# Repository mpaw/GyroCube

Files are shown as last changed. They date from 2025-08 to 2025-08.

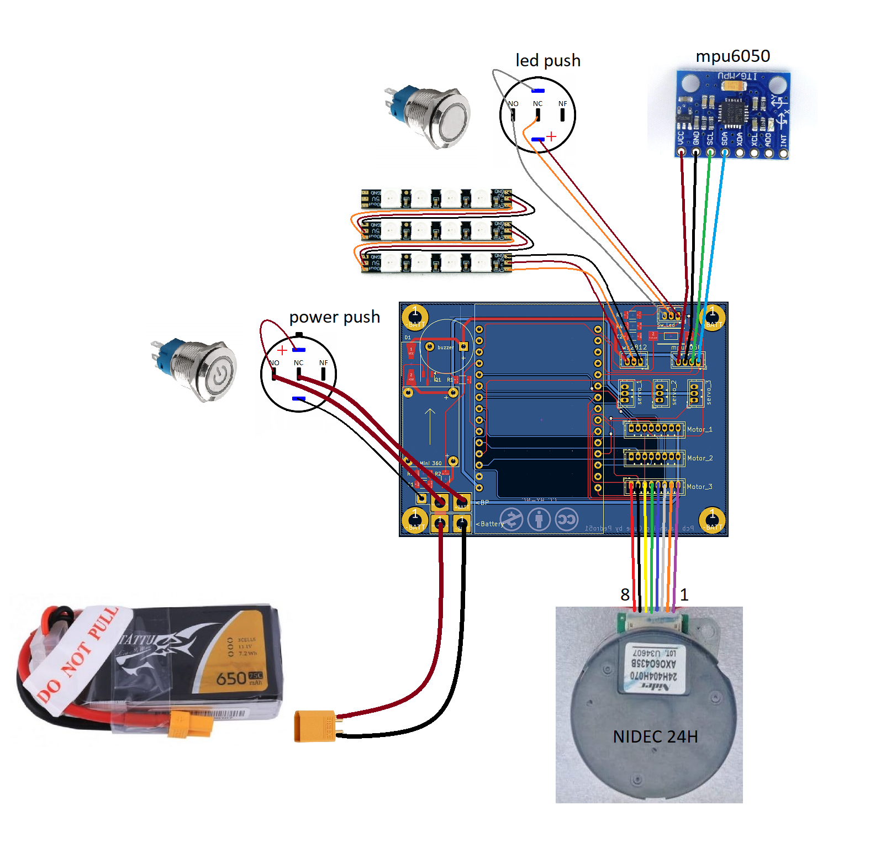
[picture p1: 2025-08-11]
PCB&Schemas/Wiring diagram.PNG

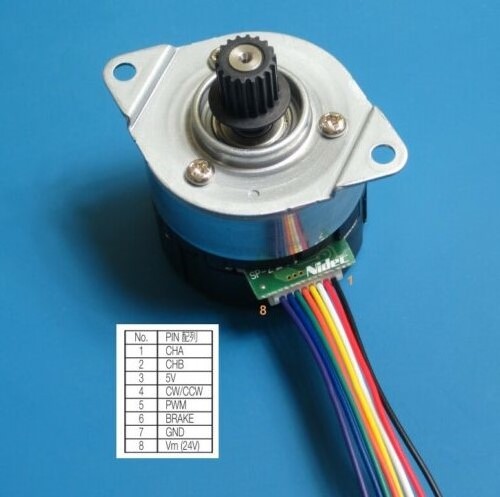
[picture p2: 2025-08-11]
PCB&Schemas/nidec.jpg

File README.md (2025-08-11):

# GyroCube
Self Balancing Cube Project

Balancing Cube project based on the "remrc" model: https://www.thingiverse.com/thing:6695891

    Creation of an Application to facilitate calibration and motor testing,
    Merging the main program with the motors test program,
    Creation of a printed circuit for those who wish to have a beautiful object,
    Addition of a Power button,
    Addition of a button to turn on the LEDs and change their colors,
    Modified the face files for placing the switches in 12 and 16mm. Thanks to dinomight.

Explanatory video: https://youtu.be/zuOgj580Nhk<br>
Led function video: https://youtu.be/vczHyelNjr4<br>
PCB: https://www.pcbway.com/project/shareproject/GyroCube_v1_1_5d583cf0.html<br>
Android app: [French](Appli%20APK/Cube_1_01_fr.apk),[English](Appli%20APK/Cube_1_01_en.apk)<br>
Browser BLE Config Tool: https://Pedro-51.github.io/GyroCube

#######################################################################################

For the program to work, you need to install esp32 by expressif v2.0.17 board version

#######################################################################################

## 12-5-2024 (Dinomight/Darkmadda)

Added new [BLE firmware](esp32_cube_vBLE_en/) this has a browser based config tool (can be use on android/mac/pc via chrome). The firmware is written to be used with platformio rather than the arduino ide. it may still work the arduino ide but i'm not sure (Platformio is far superior anyways). This firmware is backwards compatible with other app config methods (Bluetooth Serial, Pedro android app). I however think the new BLE tool is superior. I'm a little biased but try it you'll see.

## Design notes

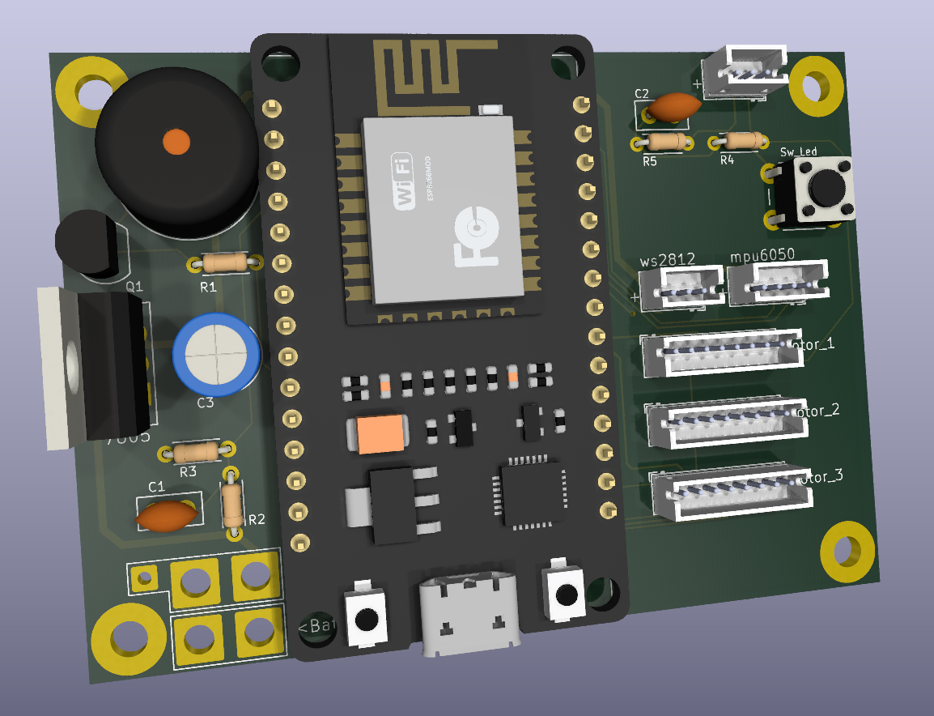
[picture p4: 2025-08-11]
PCB&Schemas/PCB_Std/3D_Std.PNG

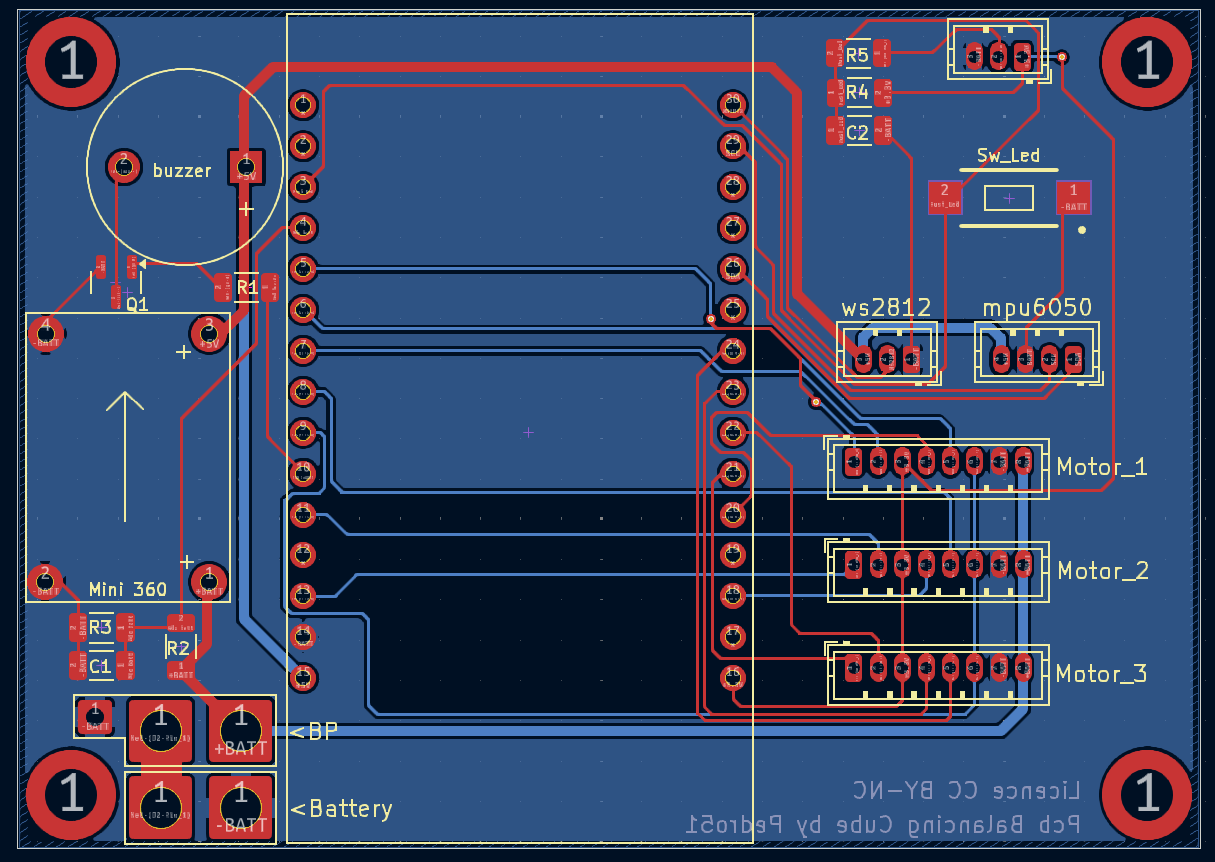
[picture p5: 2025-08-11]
PCB&Schemas/PCB_Smd/PCB_Smd.PNG

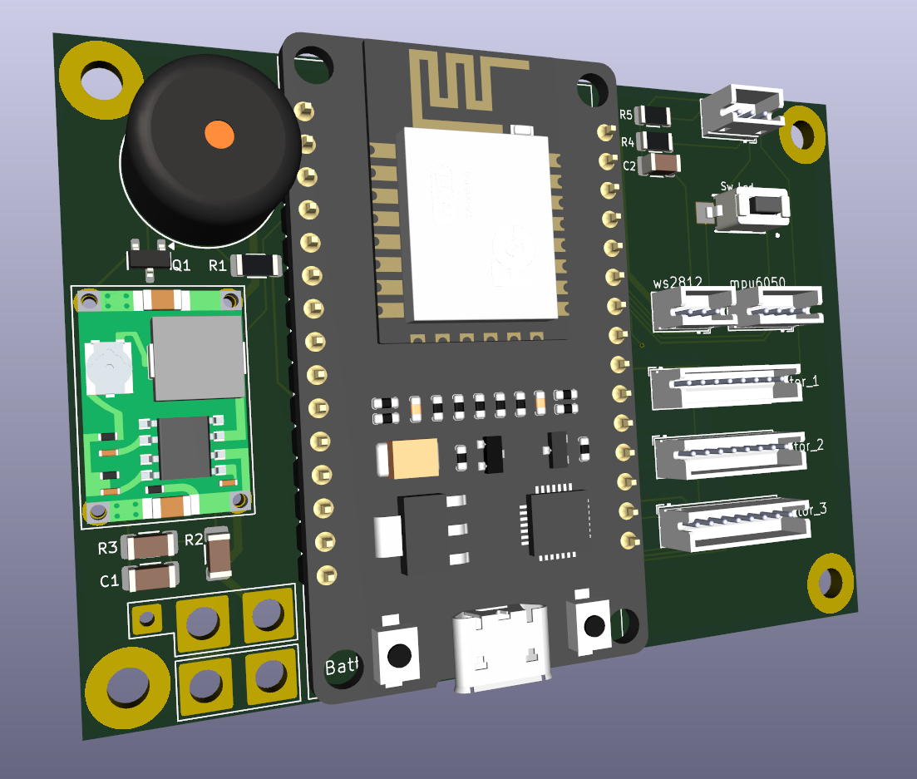
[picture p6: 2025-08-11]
PCB&Schemas/PCB_Smd/3D_Smd.png

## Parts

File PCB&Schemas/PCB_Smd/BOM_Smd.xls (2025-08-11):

Reference | Packages | Value | Qty | Comments
BT1 |  | Battery lipo 3s 650mah | 1
BZ1 |  | Buzzer 5v | 1
C1,C2 | 1206 SMD | 100nf | 2
J6,J7,J8 | JST-ZH 15cm | Connector jst-zh 01x08 double head | 3
J13 | JST-ZH 10cm | Connector jst-zh 01x03 with wire | 1
J12 | JST-ZH 10cm | Connector jst-zh 01x04 with wire | 1
Q1 | Sot-23-3 | MMBT2222A | 1
R1,R5 | 1206 SMD | 1k | 2
R2 | 1206 SMD | 33k | 1
R3,R4 | 1206 SMD | 10k | 2
SW1 | Ø16mm or Ø12mm 12-24v | Latch power inox switch | 1
SW2-1 | Ø16mm or Ø12mm 3-6v | Momentary inox switch | 1
SW2-2 |  | SMD switch reset Push | 1
U1 | mini360 | DC-DC 5v step down | 1
U2 | 30pin-micro module | esp32-wroom-32D cp2102 | 1
PCB | PCBway | PCB by Pedro51 | 1 | GyroCube_v1_2_Smd (https://www.pcbway.com/project/shareproject/GyroCube_v1_1_5d583cf0.html)
Wire | Silicon black wire | 16 AWG 100mm | 1
Wire | Silicon red wire | 16 AWG 100mm | 1
Wire | Silicon black wire | 24 AWG 100mm | 1
MPU6050 |  | Gyroscope | 1
WS1812 Led | Strip pcb for drone | Leds RGB PandaRC | 1
NIDEC 24H |  | Encoder Motor | 3
Battery Plug | Male | XT30 | 1
Screws | countersunk head screws | M4x8mm | 72
Screws | round head screw | M4x10mm | 12
Nuts | - | M4 | 144
Screws | countersunk head screws | M3x10mm | 36
Screws | countersunk head screws | M3x14mm | 12
Nuts | - | M3 | 52

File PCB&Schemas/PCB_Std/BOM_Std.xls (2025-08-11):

Reference | Packages | Value | Qty | Comments
BT1 |  | Battery lipo 3s 650mah | 1
BZ1 |  | Buzzer 5v | 1
C1,C2 | ceramic | 100nf-50v | 2
C3 | Polarized chimic | 100uf-10v | 1
J6,J7,J8 | JST-ZH 15cm | Connector jst-zh 01x08 double head | 3
J13 | JST-ZH 10cm | Connector jst-zh 01x03 with wire | 1
J12 | JST-ZH 10cm | Connector jst-zh 01x04 with wire | 1
Q1 | TO92 | 2n2222 | 1
R1,R5 | 1/4w | 1k | 2
R2 | 1/4w | 33k | 1
R3,R4 | 1/4w | 10k | 2
SW1 | Ø16mm or Ø12mm 12-24v | Latch power inox switch | 1
SW2-1 | Ø16mm or Ø12mm 3-6v | Momentary inox switch | 1
SW2-2 |  | switch reset Push | 1
U1 | TO220 | LM7805 DC-DC 5v regulator | 1
U2 | 30pin-micro module | esp32-wroom-32D cp2102 | 1
PCB | PCBway | PCB by Pedro51 | 1 | GyroCube_v1_2_Std (https://www.pcbway.com/project/shareproject/GyroCube_v1_2_Smd_9171484b.html)
Wire | Silicon black wire | 16 AWG 100mm | 1
Wire | Silicon red wire | 16 AWG 100mm | 1
Wire | Silicon black wire | 24 AWG 100mm | 1
MPU6050 |  | Gyroscope | 1
WS1812 Led | Strip pcb for drone | Leds RGB PandaRC | 1
NIDEC 24H |  | Encoder Motor | 3
Battery Plug | Male | XT30 | 1
Screws | countersunk head screws | M4x8mm | 72
Screws | round head screw | M4x10mm | 12
Nuts | - | M4 | 144
Screws | countersunk head screws | M3x10mm | 36
Screws | countersunk head screws | M3x14mm | 12
Nuts | - | M3 | 52

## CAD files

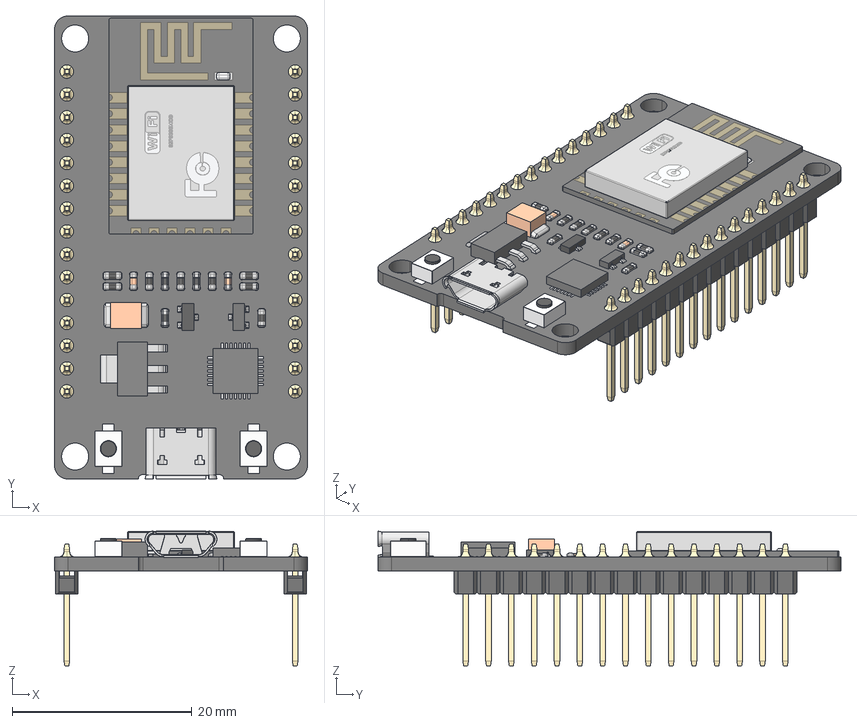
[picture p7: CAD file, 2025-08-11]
PCB&Schemas/PCB_Smd/Kidad_PCB_Smd/3d_Model/esp32_dev_kit_v1_asm.stp
28.1 x 51.5 x 15.0 mm
PCB
PIN x 30
WIFI_CARD_2
RECTANGULARCHIP_2
MICROCHIP_2
TANCHIP_2
TRANSISTOR_3-LEG_2
RESISTOR1_2 x 11
RESISTOR2-32_2 x 2
TRANSISTOR_3-LEG2_2
BUTTONFLASH-13_2 x 2
BUTTONFLASH-14_2 x 2
USB_SOCKET_2

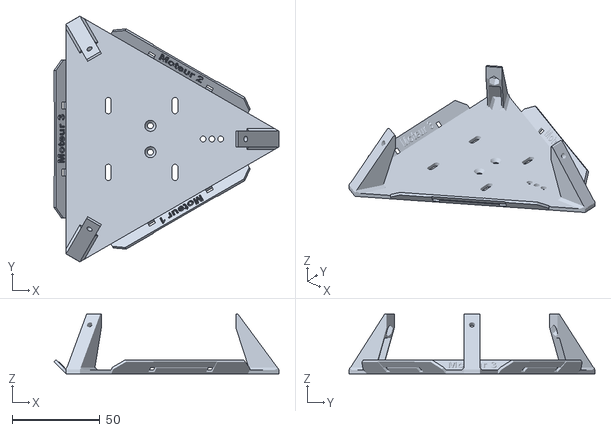
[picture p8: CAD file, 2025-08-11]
3D_files/cubli_midplate_v3_1x.stl
128.1 x 139.9 x 34.1

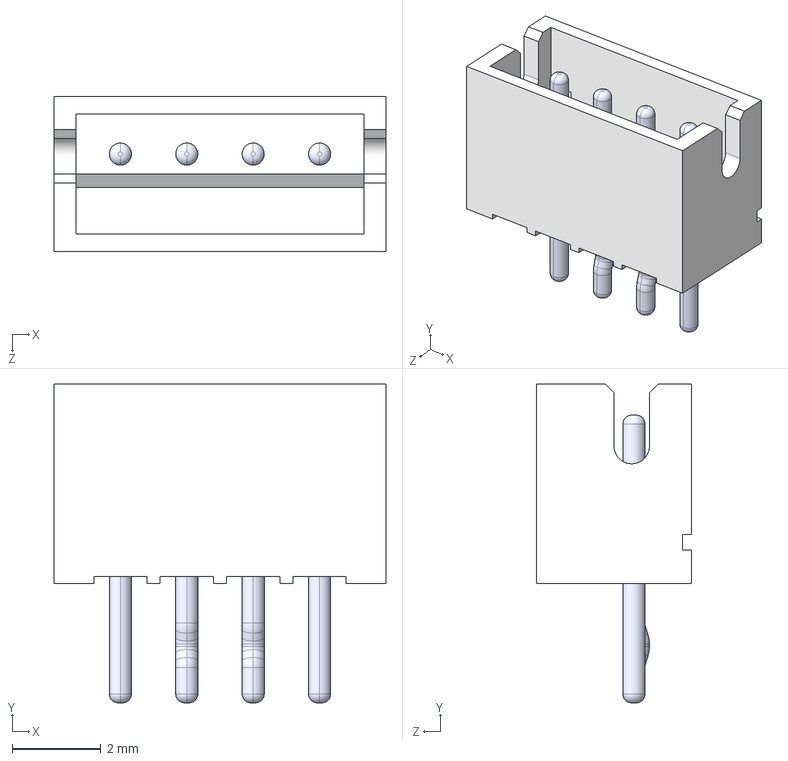
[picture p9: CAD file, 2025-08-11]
PCB&Schemas/PCB_Smd/Kidad_PCB_Smd/3d_Model/B4B-ZR--3DModel-STEP-56544.STEP
7.50 x 7.20 x 3.50 mm
BxB-ZR_4
pin_straight x 2
pin_Bent x 2

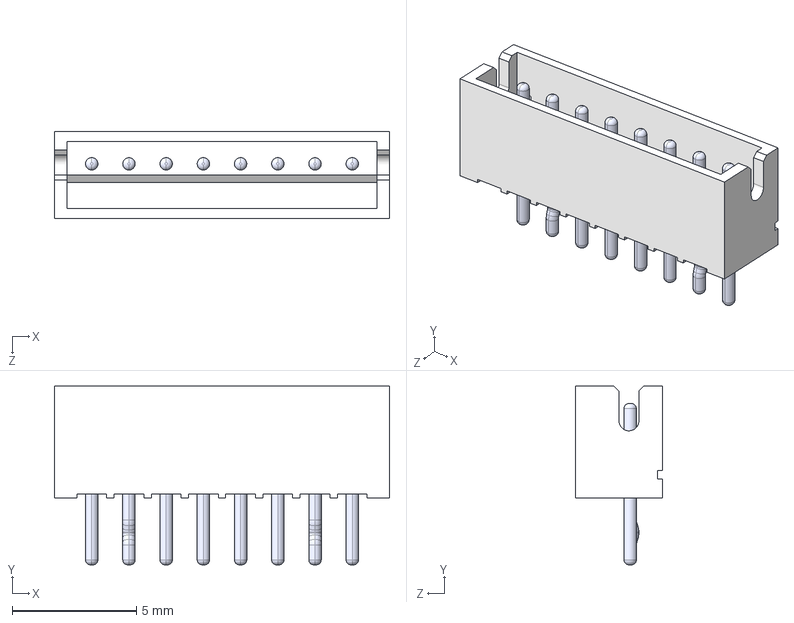
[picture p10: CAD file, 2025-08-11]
PCB&Schemas/PCB_Std/Kicad_PCB_Std/3d_Model/B8B-ZR -LF--SN---3DModel-STEP-56544.STEP
13.5 x 7.20 x 3.50 mm
BxB-ZR_8
pin_straight x 6
pin_Bent x 2

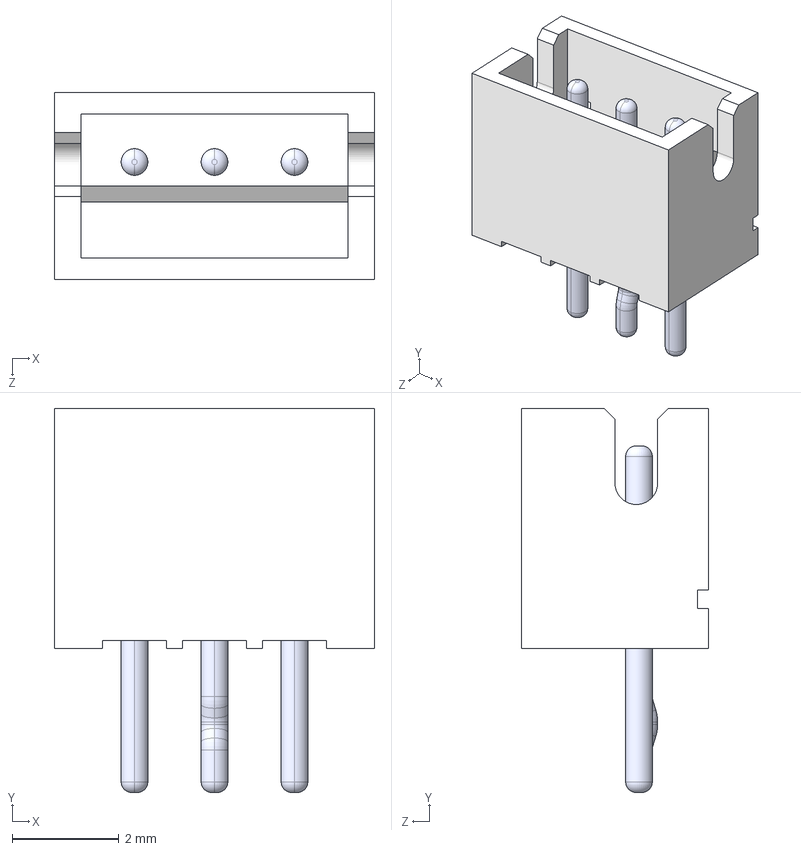
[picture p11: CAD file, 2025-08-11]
PCB&Schemas/PCB_Smd/Kidad_PCB_Smd/3d_Model/B3B-ZR--3DModel-STEP-56544.STEP
6.00 x 7.20 x 3.50 mm
BxB-ZR_3
pin_straight x 2
pin_Bent

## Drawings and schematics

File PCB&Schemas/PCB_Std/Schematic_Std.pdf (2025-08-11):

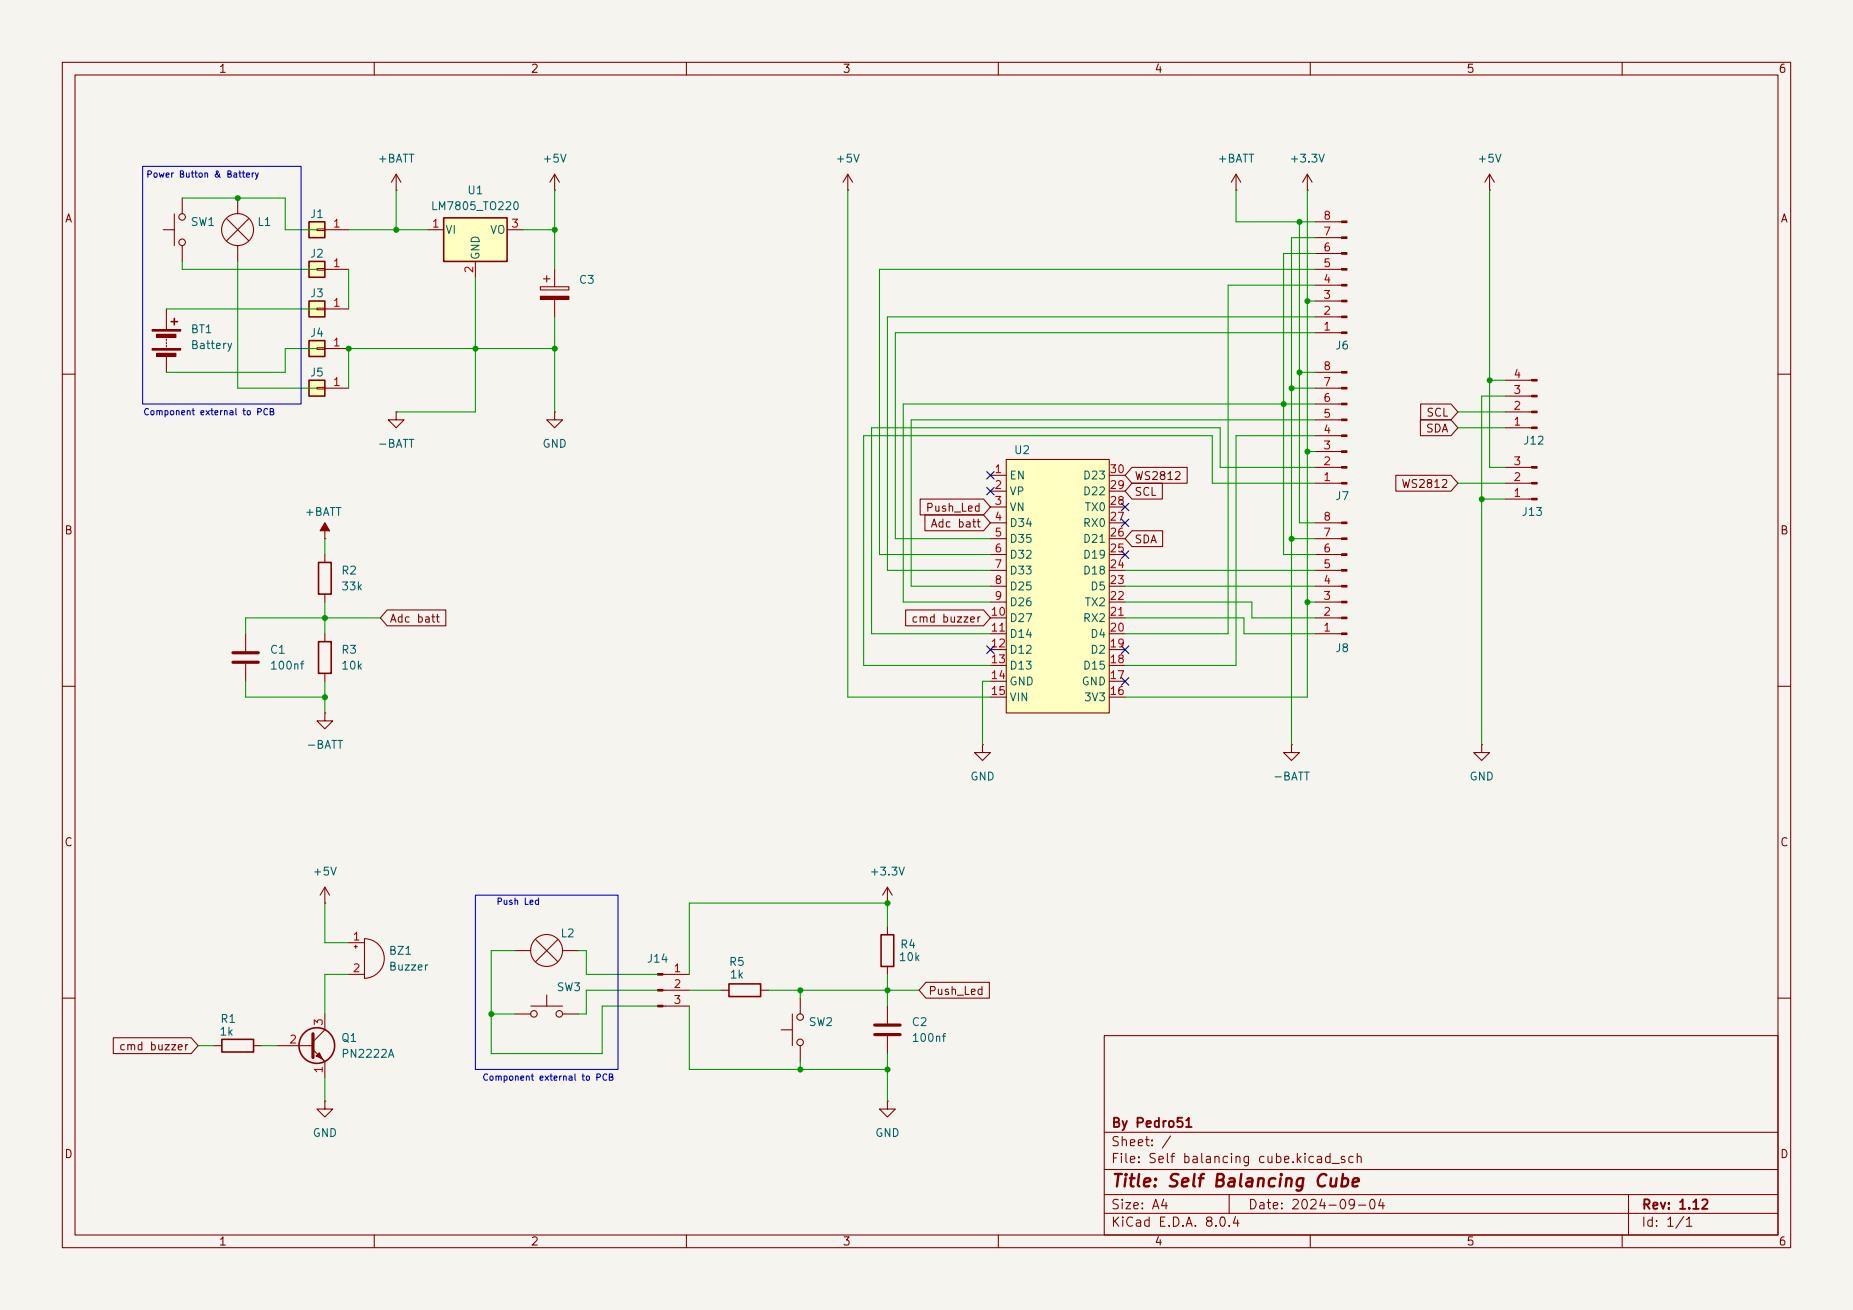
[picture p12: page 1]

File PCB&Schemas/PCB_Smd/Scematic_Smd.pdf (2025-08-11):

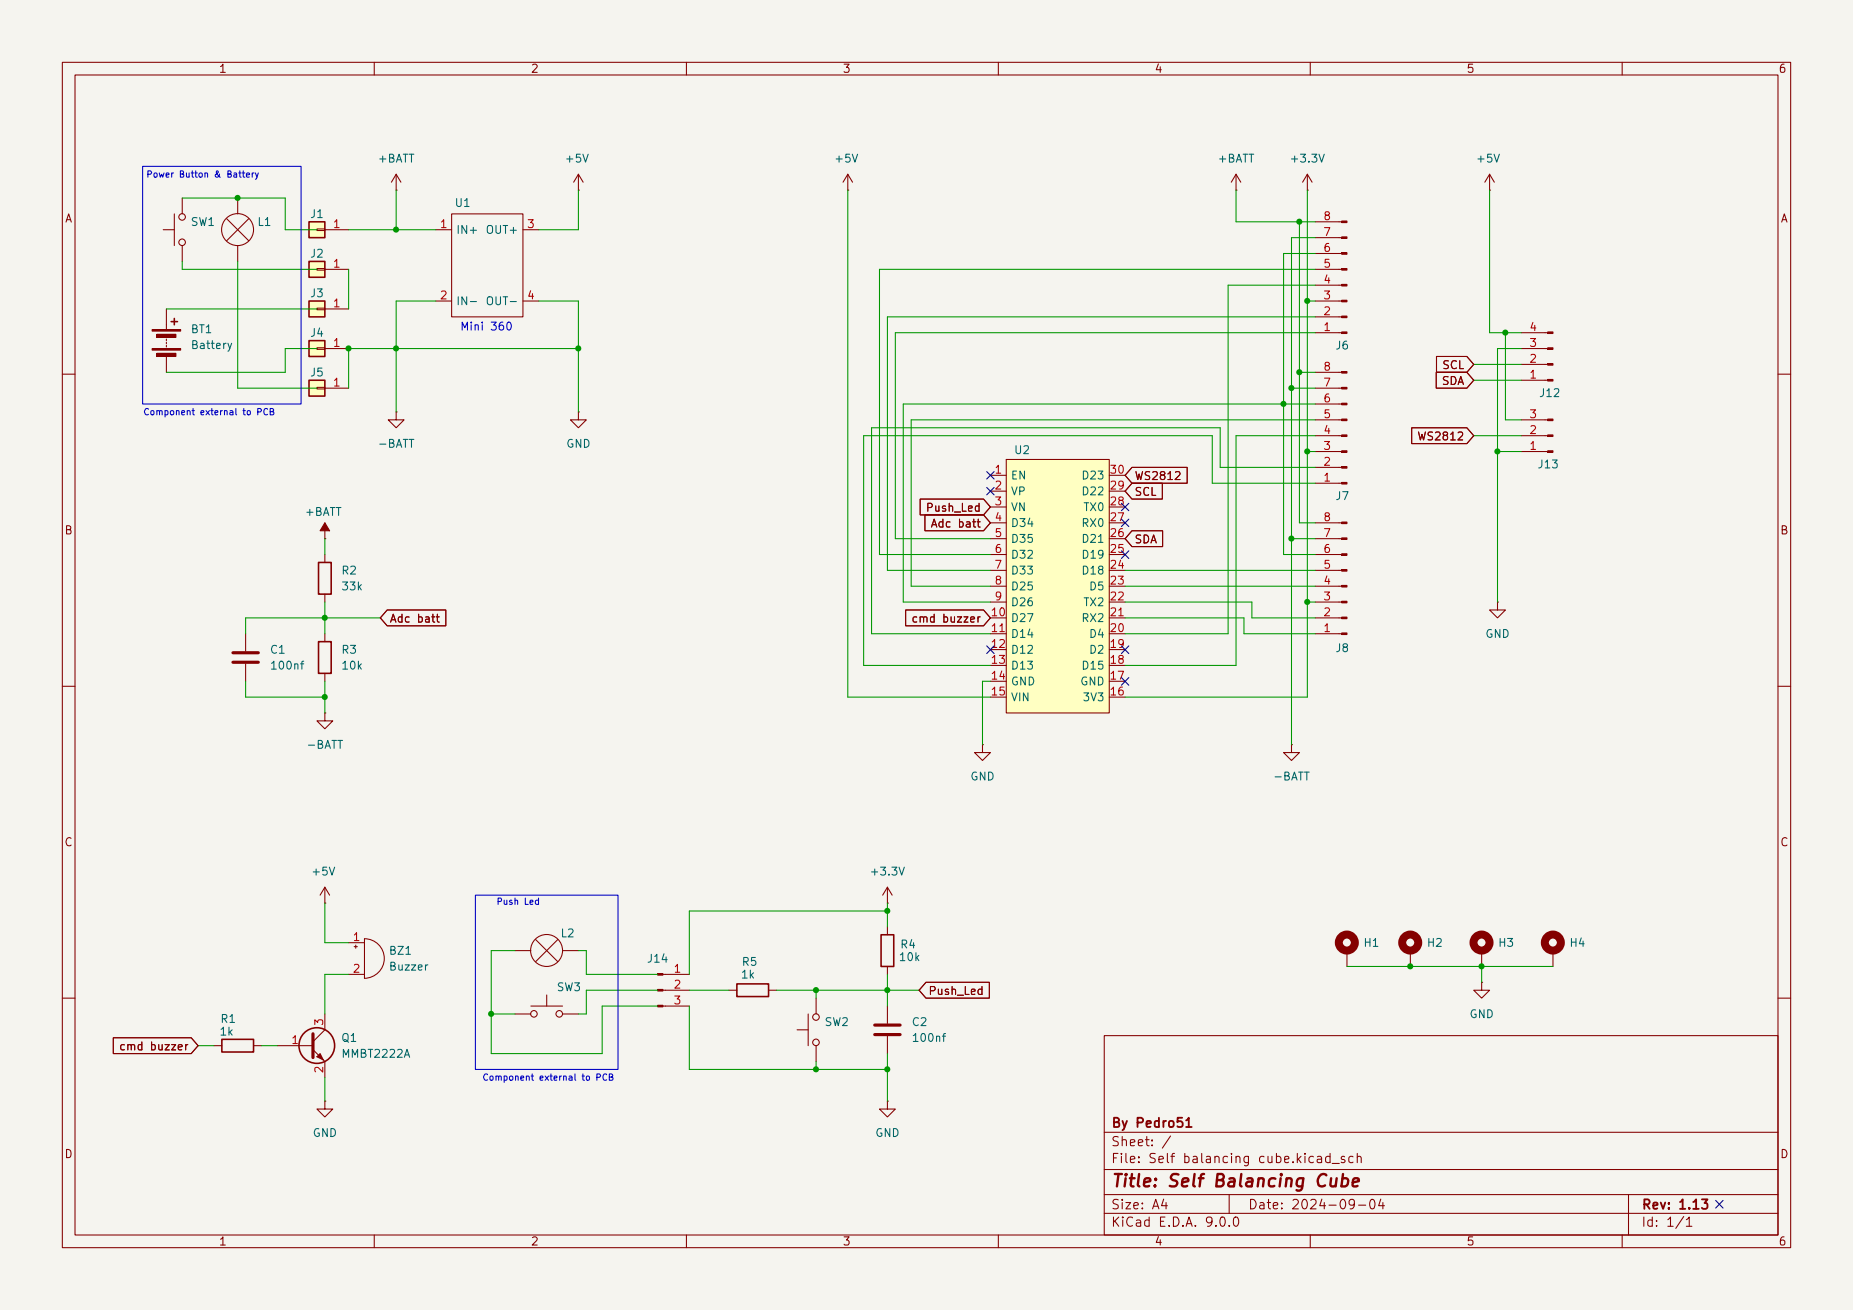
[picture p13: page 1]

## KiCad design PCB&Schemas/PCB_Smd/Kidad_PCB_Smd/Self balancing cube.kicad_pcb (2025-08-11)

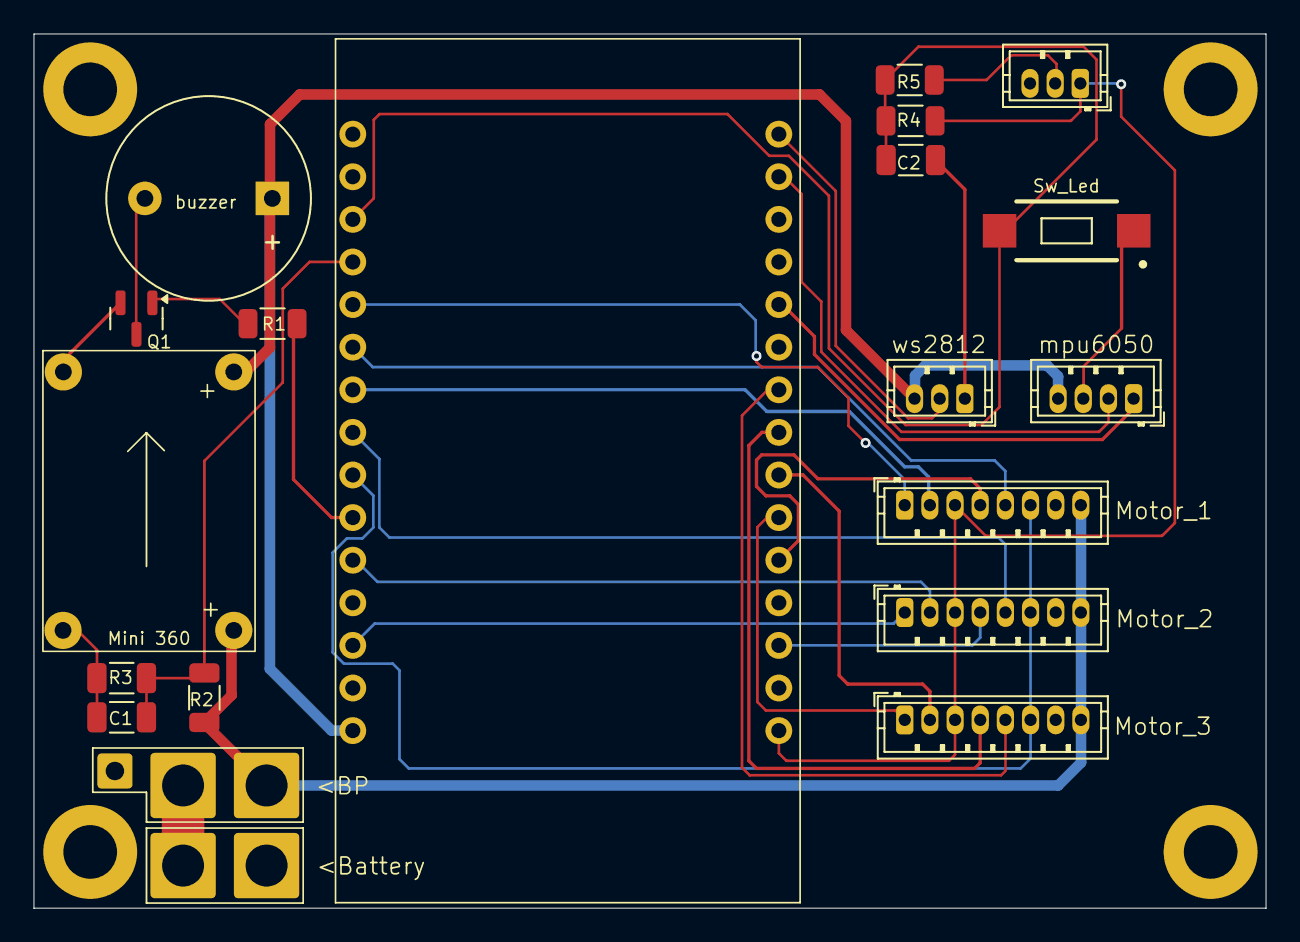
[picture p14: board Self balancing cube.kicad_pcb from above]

Board: 2 copper layers, 73.5 x 52.1 mm, 27 parts (0 on the bottom side), 27 nets.

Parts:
BZ1: Buzzer; Buzzer_12x9.5RM7.6
C1, C2: 100nf; C_1206_3216Metric
H1, H2, H3, H4: MountingHole; MountingHole_3.2mm_M3_DIN965_Pad
J1, J2, J3, J4: Conn_01x01; SolderWire-2sqmm_1x01_D2mm_OD3.9mm
J5: Conn_01x01; SolderWire-0.5sqmm_1x01_D0.9mm_OD2.1mm
J6, J7, J8: Conn_01x08_Pin; JST_ZH_B8B-ZR_1x08_P1.50mm_Vertical
J12: Conn_01x04_Pin; JST_ZH_B4B-ZR_1x04_P1.50mm_Vertical
J13, J14: Conn_01x03_Pin; JST_ZH_B3B-ZR_1x03_P1.50mm_Vertical
Q1: MMBT2222A; SOT-23
R1, R5: 1k; R_1206_3216Metric
R2: 33k; C_1206_3216Metric
R3: 10k; C_1206_3216Metric
R4: 10k; R_1206_3216Metric
SW2: SW_Push; SW_RS-032G05A3-SMRT
U1: 5v; DCDC buck
U2: esp module 30pins

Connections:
+3.3V: J6.3, J7.3, J8.3, J14.1, R4.2, U2.16 (3V3)
+5V: BZ1.1 (+), J12.4, J13.3, U1.3 (OUT+), U2.15 (VIN)
+BATT: J1.1, J6.8, J7.8, J8.8, R2.1, U1.1 (IN+)
-BATT: C1.2, C2.2, H1.1, H2.1, H3.1, H4.1, J4.1, J5.1, J6.7, J7.7, J8.7, J12.3, J13.1, J14.3, Q1.2 (E), R3.2, SW2.1, U1.2 (IN-), U1.4 (OUT-), U2.14 (GND)
Adc batt: C1.1, R2.2, R3.1, U2.4 (D34)
unnamed: BZ1.2 (-), Q1.3 (C)
unnamed: J2.1, J3.1
unnamed: J6.1, U2.5 (D35)
unnamed: J6.2, U2.7 (D33)
unnamed: J6.4, U2.20 (D4)
unnamed: J6.5, U2.6 (D32)
unnamed: J6.6, J7.6, J8.6, U2.9 (D26)
unnamed: J7.1, U2.13 (D13)
unnamed: J7.2, U2.11 (D14)
unnamed: J7.4, U2.18 (D15)
unnamed: J7.5, U2.8 (D25)
unnamed: J8.1, U2.21 (RX2)
unnamed: J8.2, U2.22 (TX2)
unnamed: J8.4, U2.23 (D5)
unnamed: J8.5, U2.24 (D18)
unnamed: J14.2, R5.1
unnamed: Q1.1 (B), R1.2
Push_Led: C2.1, R4.1, R5.2, SW2.2, U2.3 (VN)
SCL: J12.2, U2.29 (D22)
SDA: J12.1, U2.26 (D21)
WS2812: J13.2, U2.30 (D23)
cmd buzzer: R1.1, U2.10 (D27)

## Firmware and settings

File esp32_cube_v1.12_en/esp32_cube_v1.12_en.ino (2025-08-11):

#include "ESP32.h"
#include <Wire.h>
#include <EEPROM.h>
#include "BluetoothSerial.h"
#include <FastLED.h>

BluetoothSerial SerialBT; 
CRGB leds[NUM_PIXELS];

void setup() {
  Serial.begin(115200);
  SerialBT.begin("ESP32-Cube");
  EEPROM.begin(EEPROM_SIZE);
  
  FastLED.addLeds<WS2812B, LED_PIN, RGB>(leds, NUM_PIXELS);  // GRB ordering is typical
  
  pinMode(BUZZER, OUTPUT);
  pinMode(BRAKE, OUTPUT);
  digitalWrite(BRAKE, HIGH);
  pinMode(INT_LED, INPUT);

  for (i=0;i<250;i+=10){ colorLed(i, i, 0, 1, 12, 0);}
  for (RGB_val=0;RGB_val<18;RGB_val++){
    Red = RGB_Color[RGB_val][0]; Green = RGB_Color[RGB_val][1]; Blue  = RGB_Color[RGB_val][2];
    colorLed(Red, Green, Blue, 1, 12, 80); //Red, Green, Blue, FirstPixel, LastPixel, Delay
  }
  for (i=250;i>0;i-=10){colorLed(i, i*0.68, 0, 1, 12, 5);}
  colorLed(0, 0, 0, 1, 12, 0);
  
  pinMode(DIR1, OUTPUT);
  pinMode(ENC1_1, INPUT);
  pinMode(ENC1_2, INPUT);
  attachInterrupt(ENC1_1, ENC1_READ, CHANGE);
  attachInterrupt(ENC1_2, ENC1_READ, CHANGE);
  ledcSetup(PWM1_CH, BASE_FREQ, TIMER_BIT);
  ledcAttachPin(PWM1, PWM1_CH);
  Motor1_control(0);
  
  pinMode(DIR2, OUTPUT);
  pinMode(ENC2_1, INPUT);
  pinMode(ENC2_2, INPUT);
  attachInterrupt(ENC2_1, ENC2_READ, CHANGE);
  attachInterrupt(ENC2_2, ENC2_READ, CHANGE);
  ledcSetup(PWM2_CH, BASE_FREQ, TIMER_BIT);
  ledcAttachPin(PWM2, PWM2_CH);
  Motor2_control(0);
  
  pinMode(DIR3, OUTPUT);
  pinMode(ENC3_1, INPUT);
  pinMode(ENC3_2, INPUT);
  attachInterrupt(ENC3_1, ENC3_READ, CHANGE);
  attachInterrupt(ENC3_2, ENC3_READ, CHANGE);
  ledcSetup(PWM3_CH, BASE_FREQ, TIMER_BIT);
  ledcAttachPin(PWM3, PWM3_CH);
  Motor3_control(0);

  EEPROM.get(0, offsets);
  //offsets.ID = 0; // for debug
  if(offsets.ID == 255){
    offsets.ID = 0;
    offsets.Red = Red; offsets.Green = Green; offsets.Blue = Blue; offsets.RGB_val = RGB_val;
    offsets.K1 = K1; offsets.K2 = K2; offsets.K3 = K3; offsets.K4 = K4; offsets.zK2 = zK2; offsets.zK3 = zK3;
    offsets.eK1 = eK1; offsets.eK2 = eK2; offsets.eK3 = eK3; offsets.eK4 = eK4;
    save();
  }else if (offsets.ID == 96){
    Red = offsets.Red; Green = offsets.Green; Blue = offsets.Blue;
    K1 = offsets.K1; K2 = offsets.K2; K3 = offsets.K3; K4 = offsets.K4; zK2 = offsets.zK2; zK3 = offsets.zK3;
    eK1 = offsets.eK1; eK2 = offsets.eK2; eK3 = offsets.eK3; eK4 = offsets.eK4;
    calibrated = true;
  }

  angle_setup();
}

void loop() {
  currentT = millis();
  if (currentT - previousT_1 >= loop_time) {
    Tuning();
    angle_calc();
        
    motor1_speed = enc_count1;
    enc_count1 = 0;
    motor2_speed = enc_count2;
    enc_count2 = 0;
    motor3_speed = enc_count3;
    enc_count3 = 0;
    

  if (Mode == 0){

    threeWay_to_XY(motor1_speed, motor2_speed, motor3_speed);
    motors_speed_Z = motor1_speed + motor2_speed + motor3_speed;
    
    if (vertical_vertex && calibrated && !calibrating) {    
      digitalWrite(BRAKE, HIGH);
      gyroX = GyX / 131.0;
      gyroY = GyY / 131.0;
      gyroZ = GyZ / 131.0;
      gyroXfilt = alpha * gyroX + (1 - alpha) * gyroXfilt;
      gyroYfilt = alpha * gyroY + (1 - alpha) * gyroYfilt;
      
      int pwm_X = constrain(K1 * robot_angleX + K2 * gyroXfilt + K3 * speed_X + K4 * motors_speed_X, -255, 255);
      int pwm_Y = constrain(K1 * robot_angleY + K2 * gyroYfilt + K3 * speed_Y + K4 * motors_speed_Y, -255, 255);
      int pwm_Z = constrain(zK2 * gyroZ + zK3 * motors_speed_Z, -255, 255);

      motors_speed_X += speed_X / 5; 
      motors_speed_Y += speed_Y / 5;
      XYZ_to_threeWay(-pwm_X, pwm_Y, -pwm_Z);
      
    } else if (vertical_edge && calibrated && !calibrating) {
      digitalWrite(BRAKE, HIGH);
      gyroX = GyX / 131.0;
      gyroXfilt = alpha * gyroX + (1 - alpha) * gyroXfilt;
      
      int pwm_X = constrain(eK1 * robot_angleX + eK2 * gyroXfilt + eK3 * motor3_speed + eK4 * motors_speed_X, -255, 255);
      
      motors_speed_X += motor3_speed / 5;
      Motor3_control(pwm_X);
      
    } else {
      XYZ_to_threeWay(0, 0, 0);
      digitalWrite(BRAKE, LOW);
      motors_speed_X = 0;
      motors_speed_Y = 0; 
      
      if  (calibrated && !calibrating) {
        RGB_Process();
      }
    }
  }

  if (Mode == 1 ){
      switch (f) {
        case 1:
          colorLed(50, 50, 50, 1, 4, 0);
          digitalWrite(BRAKE, HIGH);
          if (lock) Serial.println("Test moteur 1."); SerialBT.println("46");
          Motor1_control(50);
          break;
        case 4:
          digitalWrite(BRAKE, LOW);
          if (lock) Serial.println("Stop."); SerialBT.println("41");
          Motor1_control(0);
          break;      
        case 7:
          digitalWrite(BRAKE, HIGH);
          if (lock) Serial.println("Changement direction..."); SerialBT.println("42");
          Motor1_control(-50);
          break;
        case 10:
          digitalWrite(BRAKE, LOW);
          if (lock) Serial.println("Stop."); SerialBT.println("41");
          Motor1_control(0);
          break; 
        case 13:
          digitalWrite(BRAKE, HIGH);
          if (lock) Serial.println("Check de l'encodeur..."); SerialBT.println("43");
          Motor1_control(70);
          break; 
        case 16:
          digitalWrite(BRAKE, LOW);
          if (lock && motor1_speed > 300) {
            Serial.println("Encodeur OK."); 
            Serial.print("Vitesse: "); Serial.println(motor1_speed);
            s1.concat(motor1_speed);
            SerialBT.println("44"  + s1);
            Serial.println("Stop.");
          } else if (lock && motor1_speed <= 0) {
            Serial.println("Encodeur FAIL.");
            Serial.print("Vitesse: "); Serial.println(motor1_speed);
            s1.concat(motor1_speed);
            SerialBT.println("45"  + s1);
            Serial.println("Stop.");
          }
          s1 = "";
          Motor1_control(0);
          colorLed(0, 0, 0, 1, 4, 0);
          break;      
  
        case 19:
          colorLed(50, 50, 50, 5, 8, 0);
          digitalWrite(BRAKE, HIGH);
          if (lock) Serial.println("Test moteur 2."); SerialBT.println("47");
          Motor2_control(50);
          break;
        case 22:
          digitalWrite(BRAKE, LOW);
          if (lock) Serial.println("Stop."); SerialBT.println("41");
          Motor2_control(0);
          break;      
        case 25:
          digitalWrite(BRAKE, HIGH);
          if (lock) Serial.println("Changement direction..."); SerialBT.println("42");
          Motor2_control(-50);
          break;
        case 28:
          digitalWrite(BRAKE, LOW);
          if (lock) Serial.println("Stop."); SerialBT.println("41");
          Motor2_control(0);
          break; 
        case 31:
          digitalWrite(BRAKE, HIGH);
          if (lock) Serial.println("Check de l'encodeur..."); SerialBT.println("43");
          Motor2_control(70);
          break; 
        case 34:
          digitalWrite(BRAKE, LOW);
          if (lock && motor2_speed > 300) {
            Serial.println("Encodeur OK.");
            Serial.print("Vitesse: "); Serial.println(motor2_speed);
            s1.concat(motor2_speed);
            SerialBT.println("44"  + s1);
            Serial.println("Stop.");
          } else if (lock && motor2_speed <= 0) {
            Serial.println("Encodeur FAIL.");
            Serial.print("Vitesse: "); Serial.println(motor2_speed);
            s1.concat(motor2_speed);
            SerialBT.println("45"  + s1);
            Serial.println("Stop.");
          }
          s1 = "";
          Motor2_control(0);
          colorLed(0, 0, 0, 5, 8, 0);
          break;        
  
        case 37:
          colorLed(50, 50, 50, 9, 12, 0);
          digitalWrite(BRAKE, HIGH);
          if (lock) Serial.println("Test moteur 3."); SerialBT.println("48");
          Motor3_control(50);
          break;
        case 40:
          digitalWrite(BRAKE, LOW);
          if (lock) Serial.println("Stop."); SerialBT.println("41");
          lock = 0;
          Motor3_control(0);
          break;      
        case 43:
          digitalWrite(BRAKE, HIGH);
          if (lock) Serial.println("Changement direction..."); SerialBT.println("42");
          Motor3_control(-50);
          break;
        case 46:
          digitalWrite(BRAKE, LOW);
          if (lock) Serial.println("Stop."); SerialBT.println("41");
          Motor3_control(0);
          break; 
        case 49:
          digitalWrite(BRAKE, HIGH);
          if (lock) Serial.println("Check de l'encodeur..."); SerialBT.println("43");
          Motor3_control(70);
          break; 
        case 52:
          digitalWrite(BRAKE, LOW);
          if (lock && motor3_speed > 300) {
            Serial.println("Encodeur OK.");
            Serial.print("Vitesse: "); Serial.println(motor3_speed);
            s1.concat(motor3_speed);
            SerialBT.println("44"  + s1);
            Serial.println("Stop.");
          } else if (lock && motor3_speed <= 0) {
            Serial.println("Encodeur FAIL.");
            Serial.print("Vitesse: "); Serial.println(motor3_speed);
            s1.concat(motor3_speed);
            SerialBT.println("45"  + s1);
            Serial.println("Stop.");
          }
          s1 = "";
          Motor3_control(0);
          colorLed(0, 0, 0, 9, 12, 0);
          break;        
        }
        lock = 0;
  }
    
  previousT_1 = currentT;
}    
  if (currentT - previousT_2 >= 1000) {

    battVoltage((double)analogRead(VBAT) / 204); // value 204 must be selected by measuring battery voltage!
    
    if (!calibrated && !calibrating) {
      Serial.println("Tu doit d'abord procéder au calibrage des points d'équilibres...");
      SerialBT.println("95");
      if (!calibrated_leds) {
        colorLed(0, 50, 0, 1, 12, 0); 
        calibrated_leds = true; 
      } else {
         (0, 0, 0, 1, 12, 0); 
        calibrated_leds = false; 
      }
    }
    
    if (Mode == 1){
      f++; 
      if (f == 53){ beep(); Serial.println("Fin des tests Moteurs."); SerialBT.println("96"); f = 1; Mode = 0;} 
    lock = 1;
    }
    previousT_2 = currentT;
  }
  
  if (ConnectBT == true && (currentT - previousT_3) > DelayBT)
      {
        init_BT();
        ConnectBT = false;
      }
}

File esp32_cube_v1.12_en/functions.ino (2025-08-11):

void writeTo(byte device, byte address, byte value) {
  Wire.beginTransmission(device);
  Wire.write(address);
  Wire.write(value);
  Wire.endTransmission(true);
}

void beep() {
    digitalWrite(BUZZER, HIGH);
    delay(2);
    digitalWrite(BUZZER, LOW);
    delay(80);
}
    
//***********************************************************************
// Initialise Bluetooth
//***********************************************************************
void init_BT()
{
        Mode = 0; loop_time = 15;
        calibrating = false;
        colorLed(0, 0, 0, 1, 12, 0);
        LedRGB = false;
}

//***********************************************************************
// Rgb Led Command
//***********************************************************************
void colorLed(int Red, int Green, int Blue , int firstled, int lastled, int wait) {
    for(int i = firstled-1; i < lastled; i++) {    // For each pixel in strip...
    leds[i] = CRGB(Red, Green, Blue);
    FastLED.show();                          //  Update strip to match
  }
    delay(wait);                           //  Pause for a moment
}

//***********************************************************************
// Rgb Led Process
//***********************************************************************
void RGB_Process(){
  j = 0;
  while (digitalRead(INT_LED) == LOW){
    if (Push == false){Push = true;}
    j++; delay (5);
    if (j >= 250){break;}
  }
  if (!ChooseColor){
    if (Push == true){
      if (j < 250){
        if (LedRGB == true){
          colorLed(0, 0, 0, 1, 12, 0);
          LedRGB = false;
        }else{
          colorLed(Red, Green, Blue, 1, 12, 0);
          LedRGB = true;
        }
        beep();
      }else{
        Push = false; LedRGB = true; 
        colorLed(Red, Green, Blue, 1, 12, 80);
        colorLed(0, 0, 0, 1, 12, 80);
        colorLed(Red, Green, Blue, 1, 12, 0); beep ();
        while (digitalRead(INT_LED) == LOW){}
        delay (5); ChooseColor = true;
      }
    }
  }else{
    if (Push == true){
      if (j < 250){
        if (RGB_val < 17){RGB_val++;}else{RGB_val = 0;}
        Red = RGB_Color[RGB_val][0]; Green = RGB_Color[RGB_val][1]; Blue = RGB_Color[RGB_val][2];
        colorLed(Red, Green, Blue, 1, 12, 0);
        Push = false;
        beep();
      }else{
        offsets.Red = Red; offsets.Green = Green; offsets.Blue = Blue; offsets.RGB_val = RGB_val;
        save();
        colorLed(0, 0, 0, 1, 12, 0); 
        beep (); colorLed(Red, Green, Blue, 1, 12, 0); 
        beep ();
        Push = false; ChooseColor = false;
      }
    }
  }
  while (digitalRead(INT_LED) == LOW){}
  if (Push == true){Push = false;}
  delay (5);
}

void save() {
    EEPROM.put(0, offsets);
    EEPROM.commit();
    beep();
}

void angle_setup() {
  Wire.begin();
  delay (100);
  writeTo(MPU6050, PWR_MGMT_1, 0);
  writeTo(MPU6050, ACCEL_CONFIG, accSens << 3); // Specifying output scaling of accelerometer
  writeTo(MPU6050, GYRO_CONFIG, gyroSens << 3); // Specifying output scaling of gyroscope
  delay (100);
  
  beep();
  colorLed(50, 0, 0, 9, 12, 0);
  for (int i = 0; i < 512; i++) {
    angle_calc();
    GyZ_offset_sum += GyZ;
    delay(5);
  }
  GyZ_offset = GyZ_offset_sum >> 9;
  Serial.print("GyZ offset value = "); Serial.println(GyZ_offset);
  beep();
  colorLed(0, 0, 0, 9, 12, 0);

  colorLed(50, 0, 0, 5, 8, 0);
  for (int i = 0; i < 512; i++) {
    angle_calc();
    GyY_offset_sum += GyY;
    delay(5);
  }
  GyY_offset = GyY_offset_sum >> 9;
  Serial.print("GyY offset value = "); Serial.println(GyY_offset);
  beep();
  colorLed(0, 0, 0, 5, 8, 0);

  colorLed(50, 0, 0, 1, 4, 0);
  for (int i = 0; i < 512; i++) {
    angle_calc();
    GyX_offset_sum += GyX;
    delay(5);
  }
  GyX_offset = GyX_offset_sum >> 9;
  Serial.print("GyX offset value = "); Serial.println(GyX_offset);
  colorLed(0, 0, 0, 1, 4, 150);
  beep();
  beep();
  colorLed(50, 0, 0, 1, 12, 300);
  colorLed(0, 0, 0, 1, 12, 150);
  colorLed(50, 0, 0, 1, 12, 300);
  colorLed(0, 0, 0, 1, 12, 0);
}

void angle_calc() {
  
  Wire.beginTransmission(MPU6050);
  Wire.write(0x43);
  Wire.endTransmission(false);
  Wire.requestFrom(MPU6050, 6, true);  
  GyX = Wire.read() << 8 | Wire.read();
  GyY = Wire.read() << 8 | Wire.read();
  GyZ = Wire.read() << 8 | Wire.read();

  Wire.beginTransmission(MPU6050);
  Wire.write(0x3B);                  
  Wire.endTransmission(false);
  Wire.requestFrom(MPU6050, 6, true); 
  AcX = Wire.read() << 8 | Wire.read();
  AcY = Wire.read() << 8 | Wire.read();
  AcZ = Wire.read() << 8 | Wire.read();

  if (abs(AcX) < 2000) {
    AcXc = AcX - offsets.acXv;
    AcYc = AcY - offsets.acYv;
    AcZc = AcZ - offsets.acZv;
  } else {
    AcXc = AcX - offsets.acXe;
    AcYc = AcY - offsets.acYe;
    AcZc = AcZ - offsets.acZe;
  }
  GyZ -= GyZ_offset;
  GyY -= GyY_offset;
  GyX -= GyX_offset;

  robot_angleY += GyY * loop_time / 1000 / 65.536;
  Acc_angleY = atan2(AcXc, -AcZc) * 57.2958;
  robot_angleY = robot_angleY * Gyro_amount + Acc_angleY * (1.0 - Gyro_amount);

  robot_angleX += GyX * loop_time / 1000 / 65.536;
  Acc_angleX = -atan2(AcYc, -AcZc) * 57.2958;
  robot_angleX = robot_angleX * Gyro_amount + Acc_angleX * (1.0 - Gyro_amount);

  //Serial.print("AcX= "); Serial.print(AcX); Serial.print("  AcY= "); Serial.print(AcY); Serial.print("  AcZ= "); Serial.println(AcZ);
  //Serial.print("angleX= "); Serial.print(Acc_angleX); Serial.print("  angleY= "); Serial.println(Acc_angleY);
  //Serial.println(); Serial.println(); 
  
  if (abs(AcX) < 2000 && abs(Acc_angleX) < 0.4 && abs(Acc_angleY) < 0.4 && !vertical_vertex && !vertical_edge) {
    robot_angleX = Acc_angleX;
    robot_angleY = Acc_angleY;
    vertical_vertex = true;
  } else if (abs(AcX) > 7000 && abs(AcX) < 10000 && abs(Acc_angleX) < 0.3 && !vertical_vertex && !vertical_edge) {
    robot_angleX = Acc_angleX;
    robot_angleY = Acc_angleY;
    vertical_edge = true;
  } else if ((abs(robot_angleX) > 7 || abs(robot_angleY) > 7) && vertical_vertex) {
    vertical_vertex = false;
  } else if ((abs(robot_angleX) > 7 || abs(robot_angleY) > 7) && vertical_edge) {
    vertical_edge = false;
  }
}

void XYZ_to_threeWay(float pwm_X, float pwm_Y, float pwm_Z) {
  int16_t m1 = round((0.5 * pwm_X - 0.866 * pwm_Y) / 1.37 + pwm_Z);  
  int16_t m2 = round((0.5 * pwm_X + 0.866 * pwm_Y) / 1.37 + pwm_Z);
  int16_t m3 = -pwm_X / 1.37 + pwm_Z;  
  Motor1_control(m1);
  Motor2_control(m2);
  Motor3_control(m3);
}

void threeWay_to_XY(int in_speed1, int in_speed2, int in_speed3) {
  speed_X = ((in_speed3 - (in_speed2 + in_speed1) * 0.5) * 0.5) * 1.81;
  speed_Y = -(-0.866 * (in_speed2 - in_speed1)) / 1.1;
}

void battVoltage(double voltage) {
  if (voltage > 7 && voltage <= 9.6) {
    if (digitalRead(BUZZER) == LOW){
      digitalWrite(BUZZER, HIGH); 
      colorLed(0, 50, 0, 1, 12, 0);
      } else {
      digitalWrite(BUZZER, LOW); 
      colorLed(0, 0, 0, 1, 12, 0);
    }
  } else {
    digitalWrite(BUZZER, LOW);
  }
}
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

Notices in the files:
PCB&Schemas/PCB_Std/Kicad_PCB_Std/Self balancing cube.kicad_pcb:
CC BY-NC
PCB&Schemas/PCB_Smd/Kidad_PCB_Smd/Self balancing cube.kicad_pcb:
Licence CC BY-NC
